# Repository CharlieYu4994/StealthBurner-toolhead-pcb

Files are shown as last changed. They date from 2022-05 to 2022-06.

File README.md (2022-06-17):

# StealthBurner-PCB
为 Voron Design 最新的 StealthBurner 设计的集线 PCB 板

在线 BOM 表：http://blog.charlie.moe/StealthBurner-toolhead-pcb/bom/bom

## 特点
+ 自带一个 NTC 3950 10K 的热敏电阻，可以用于测试仓温
+ 使用 StealthBurner 官方的固定孔位，可以无损兼容现有打印件
+ 使用 18 根线，比直连更省线材

## 使用

### 打样
使用「gerber」文件夹内的文件即可，建议使用 1mm 板厚，10mil 最小线宽

### 接线
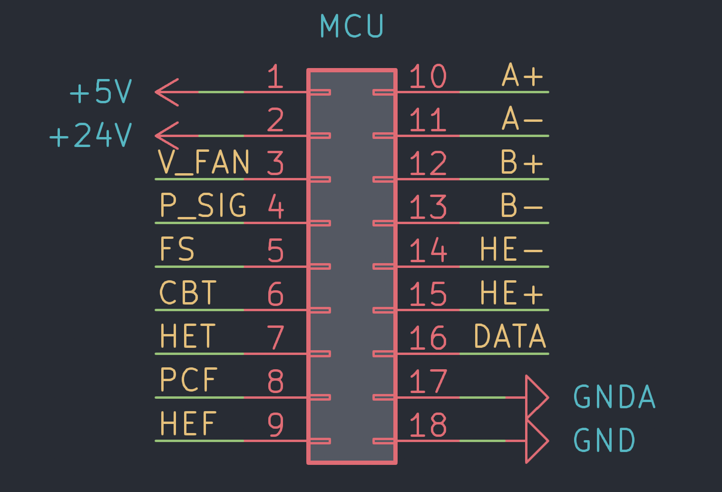
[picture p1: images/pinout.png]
pinout


1. 将 5v 连接到 LED 的 5v 电源，将 DATA 连接到 LED 信号引脚
2. 将 V_FAN 连接到你使用的风扇电源正极（两个风扇只能使用同一电压），将 PCF 和 HEF 连接到对应风扇负极
3. 将 +24v 连接到探头电源，将 P_SIG 连接到探头信号引脚
4. 将 GNDA 连接到测温接口的负极，将 CBT 和 HET 连接到对应侧温接口的正极（两个热敏电阻共地）
5. 将 A+/A-/B+/B- 连接到步进电机驱动
6. 将 HE+/HE- 连接到热端加热器接口

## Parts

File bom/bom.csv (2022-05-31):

Id | Designator | Package | Quantity | Designation | Supplier and ref
1 | J5 | JST_PH_B2B-PH-K_1x02_P2.00mm_Vertical | 1 | FS
2 | TH1 | R_0805_2012Metric | 1 | CBT
3 | J8 | JST_PH_B3B-PH-K_1x03_P2.00mm_Vertical | 1 | LED
4 | J6 | JST_PH_B2B-PH-K_1x02_P2.00mm_Vertical | 1 | HEF
5 | J9 | Molex_Micro-Fit_3.0_43045-1800_2x09_P3.00mm_Horizontal | 1 | MCU
6 | J2 | JST_PH_B4B-PH-K_1x04_P2.00mm_Vertical | 1 | E-Step
7 | J3 | Molex_Micro-Fit_3.0_43045-0200_2x01_P3.00mm_Horizontal | 1 | HE
8 | D1 | D_DO-35_SOD27_P2.54mm_Vertical_AnodeUp | 1 | BAT85
9 | J1 | JST_PH_B3B-PH-K_1x03_P2.00mm_Vertical | 1 | PROBE
10 | J4 | JST_PH_B2B-PH-K_1x02_P2.00mm_Vertical | 1 | HET
11 | J7 | JST_PH_B2B-PH-K_1x02_P2.00mm_Vertical | 1 | PCF

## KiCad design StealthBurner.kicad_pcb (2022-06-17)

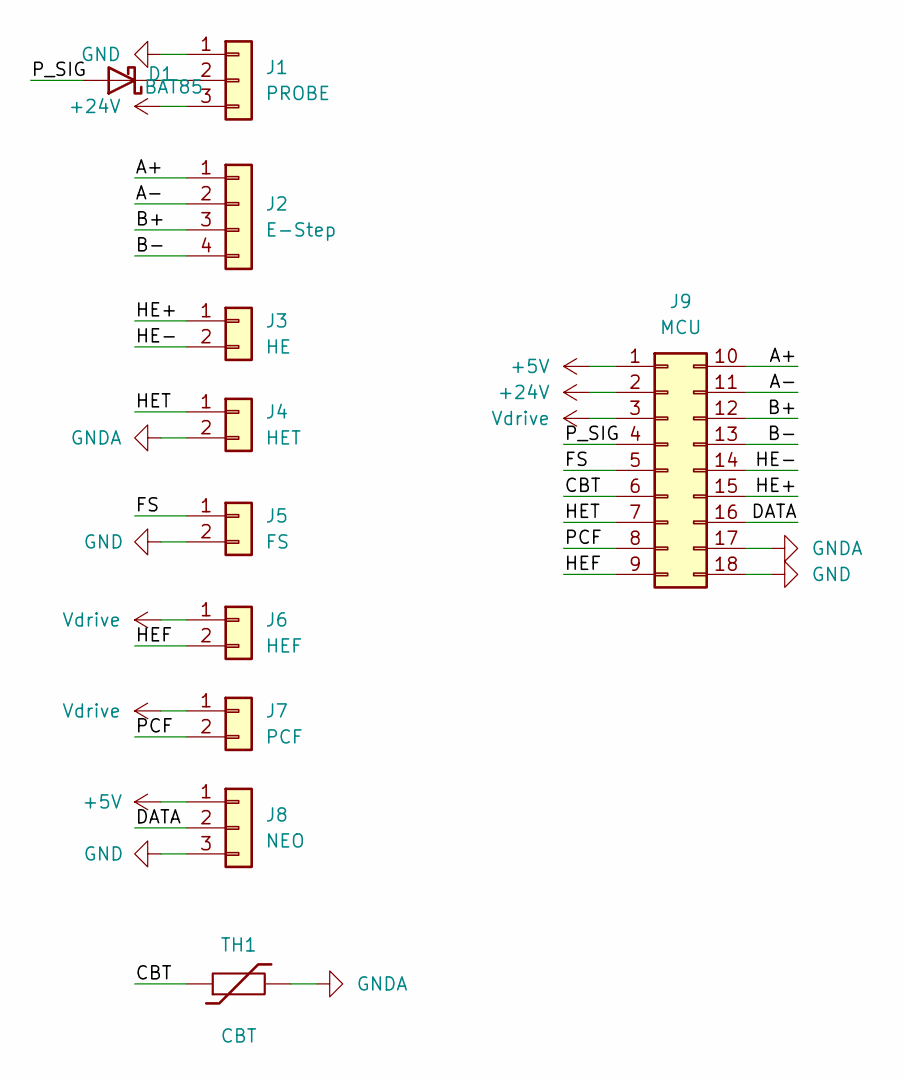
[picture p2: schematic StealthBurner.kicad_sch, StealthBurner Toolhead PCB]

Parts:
D1: BAT85; D_DO-35_SOD27_P2.54mm_Vertical_AnodeUp
J1: PROBE; JST_PH_B3B-PH-K_1x03_P2.00mm_Vertical
J2: E-Step; JST_PH_B4B-PH-K_1x04_P2.00mm_Vertical
J3: HE; Molex_Micro-Fit_3.0_43045-0200_2x01_P3.00mm_Horizontal
J4: HET; JST_PH_B2B-PH-K_1x02_P2.00mm_Vertical
J5: FS; JST_PH_B2B-PH-K_1x02_P2.00mm_Vertical
J6: HEF; JST_PH_B2B-PH-K_1x02_P2.00mm_Vertical
J7: PCF; JST_PH_B2B-PH-K_1x02_P2.00mm_Vertical
J8: NEO; JST_PH_B3B-PH-K_1x03_P2.00mm_Vertical
J9: MCU; Molex_Micro-Fit_3.0_43045-1800_2x09_P3.00mm_Horizontal
TH1: CBT; R_0805_2012Metric

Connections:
+5V: J8.1, J9.1
+24V: J1.3, J9.2
/A+: J2.1, J9.10
/A-: J2.2, J9.11
/B+: J2.3, J9.12
/B-: J2.4, J9.13
/CBT: J9.6, TH1.1
/DATA: J8.2, J9.16
/FS: J5.1, J9.5
/HE+: J3.1, J9.15
/HE-: J3.2, J9.14
/HEF: J6.2, J9.9
/HET: J4.1, J9.7
/PCF: J7.2, J9.8
/P_SIG: D1.2 (A), J9.4
GND: J1.1, J5.2, J8.3, J9.18
GNDA: J4.2, J9.17, TH1.2
unnamed: D1.1 (K), J1.2
Vdrive: J6.1, J7.1, J9.3

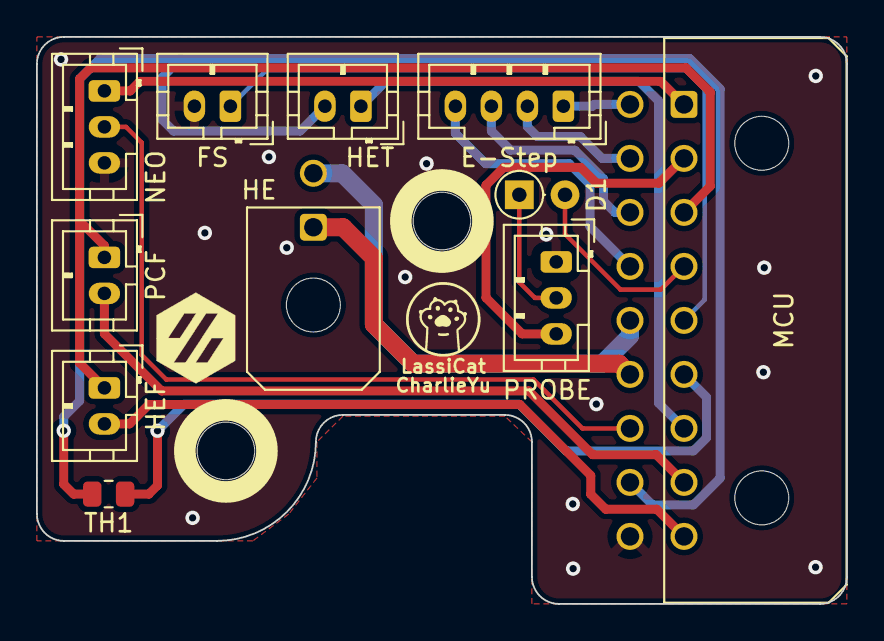
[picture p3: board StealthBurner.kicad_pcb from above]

Board: 2 copper layers, 45.0 x 31.5 mm, 15 parts (0 on the bottom side), 19 nets.

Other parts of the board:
L1: LassiCat Organization; LassiCat_Logo
L2: Voron Hex; Voron_Logo_Hex
M1, M2: M3_hole; MountingHole_3.2mm_M3_User

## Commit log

2022-05-22 Upload all the files
    [StealthBurner-B_Cu.gbr, StealthBurner-B_Mask.gbr, StealthBurner-B_Paste.gbr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]
2022-05-22 Update Logo
    [StealthBurner-B_Cu.gbr, StealthBurner-B_Mask.gbr, StealthBurner-B_Paste.gbr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]
2022-05-24 修改设计规范
    [StealthBurner.kicad_pcb, StealthBurner.kicad_sch]
2022-05-29 重新设计 PCB
    [StealthBurner.kicad_pcb, StealthBurner.kicad_sch]
2022-05-29 更新到 Beta2
    [StealthBurner.kicad_pcb]
2022-05-29 更新 Gerber 文件以及 BOM 表
    [StealthBurner-B_Cu.gbr, StealthBurner-B_Mask.gbr, StealthBurner-B_Paste.gbr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]
2022-05-29 修复 BOM
2022-05-31 添加丝印
    [StealthBurner-B_Cu.gbr, StealthBurner-B_Mask.gbr, StealthBurner-B_Paste.gbr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]
2022-05-31 添加 BOM
    [StealthBurner.kicad_pcb, bom.csv]
2022-06-02 更新到 Beta2，优化探针接口位置，优化丝印
    [StealthBurner-B_Cu.gbr, StealthBurner-B_Mask.gbr, StealthBurner-B_Paste.gbr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]
2022-06-04 微调丝印
    [StealthBurner.kicad_pcb]
2022-06-04 更新生产文件
    [StealthBurner-B_Cu.gbr, StealthBurner-B_Mask.gbr, StealthBurner-B_Paste.gbr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]
2022-06-17 增加 README 文件
2022-06-17 更改线路名称
    [StealthBurner.kicad_pcb, StealthBurner.kicad_sch]
